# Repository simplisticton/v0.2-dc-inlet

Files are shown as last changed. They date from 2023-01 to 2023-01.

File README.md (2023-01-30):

# Voron V0.2 DC Inlet Foot

Replaces the mains inlet foot part in the V0.2 to allow for the use of an external DC power supply (and consequently a 24V bed heater, since you no longer have mains power on the printer). This is based on the ["Voron 0 DC inlet" mod by arkeet](https://github.com/VoronDesign/VoronUsers/tree/master/printer_mods/arkeet/v0-dc-inlet).

## BOM
- Kycon KPJX-PM-4S connector ([Digi-Key](https://www.digikey.com/en/products/detail/kycon-inc/KPJX-PM-4S/9990081))
- Mean Well GST163A24-R7B power supply ([Digi-Key](https://www.digikey.com/en/products/detail/mean-well-usa-inc/GST160A24-R7B/7703602))
- Power switch, 20mm round, rated for at least 7A at 24VDC ([Digi-Key](https://www.digikey.com/en/products/detail/w-rth-elektronik/471002268142/9950821))
- 2x quick disconnect terminal for power switch ([Digi-Key](https://www.digikey.com/en/products/detail/te-connectivity-amp-connectors/2-520194-2/289254))
- 24V 60W bed heater ([Keenovo](https://keenovo.store/collections/standard-keenovo-silicone-heaters/products/keenovo-square-silicone-heater-3d-printer-build-plate-heatbed-heating-pad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))
- 4x M2x10 self-tapping screw
- 18AWG wire
- Heatshrink tubing

## Implications

There are several implications to not having mains power in your printer:
- 24V bed heater can be safely run at 100% power
- No need for a 24V power supply on the printer itself means a lot more availabe room 
- You can utilize a 24V-5V step down converter to power your Raspberry Pi instead of needing a separate 5V PSU

I recommend using Wago lever nuts and ferules to simplify your wiring and keep it neat and tidy!

## Instructions

1. Prepare the foot as per the Voron V0.2 manual (i.e., insert heatsets).
2. Solder the wires between the Kycon connector and the switch prior to installation. Use the quick-connect terminals on the switch side. Be sure to install heat-shrink tubing over all exposed areas (see figures 2 & 3). Also ensure that the inlet bracket is in place before soldering the connector!
3. Route the bracket, connector, and wires through the switch opening in the DC inlet foot. Don't screw the bracket to the connector until after you've run them through the switch opening -- the connector is a tight fit but if you angle it correctly it will go through! 
4. Screw the inlet bracket to the connector (see figure 4).
5. Snap the switch into place (see figure 5).
6. Screw the inlet bracket into the inlet foot (see figure 6).
7. Connect the switch to your controller board's 24DC in.

## Figures
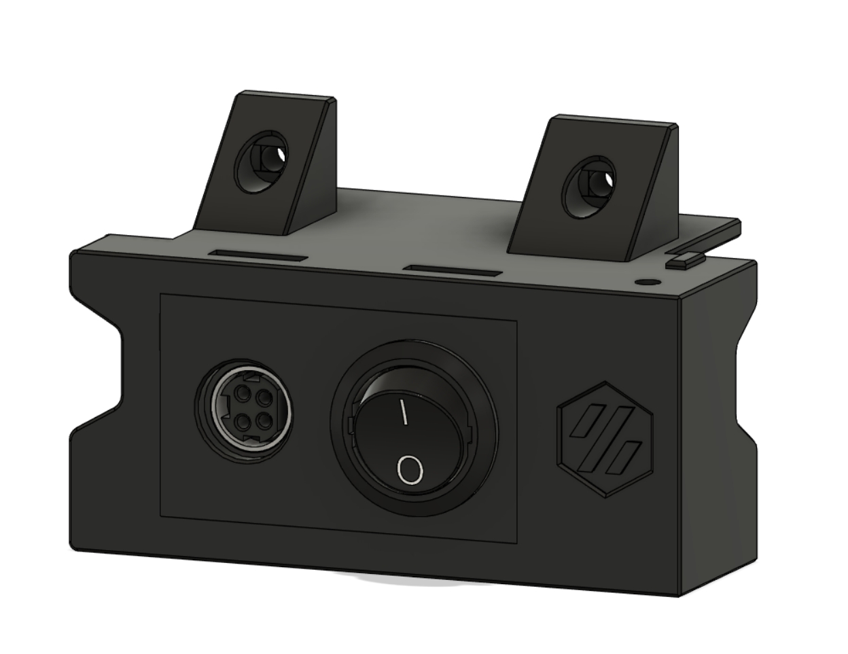
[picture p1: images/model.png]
Figure 1 - model Figure 1: Model

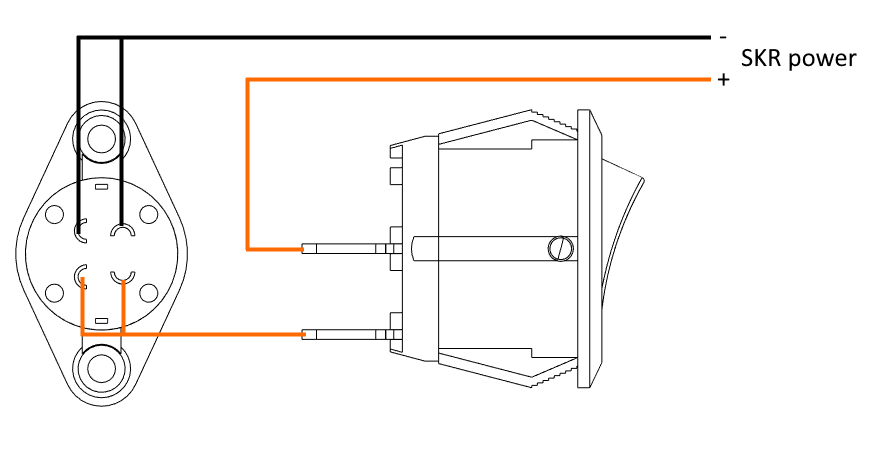
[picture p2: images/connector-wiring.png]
Figure 2 - connector wiring Figure 2: Connector Wiring

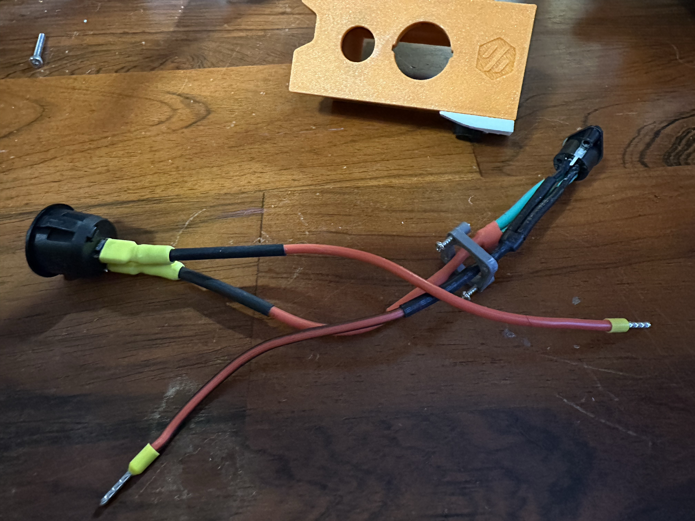
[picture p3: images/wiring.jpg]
Figure 3 - assembled wiring Figure 3: Assembled Wiring

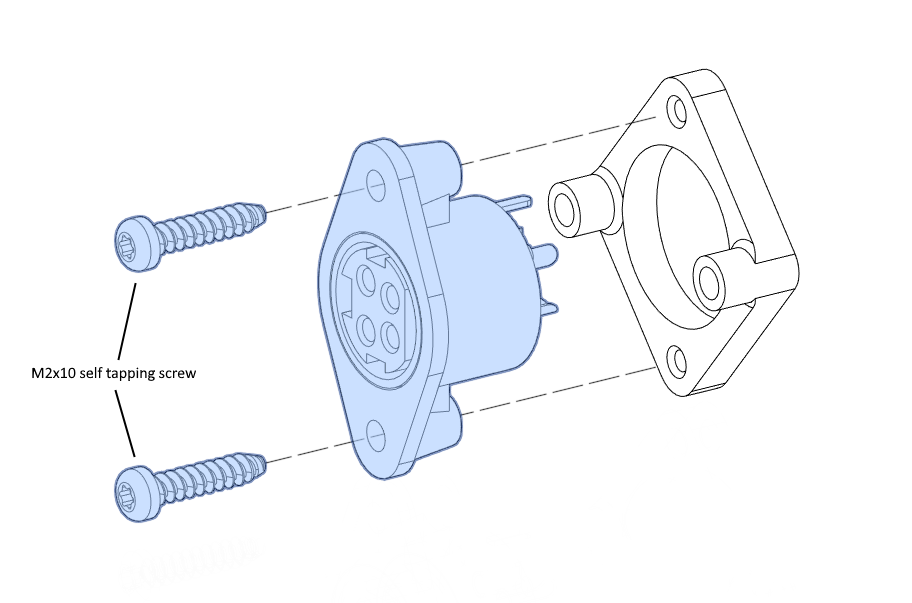
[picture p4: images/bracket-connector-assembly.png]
Figure 4 - bracket-connector assembly Figure 4: Bracket-Connector Assembly

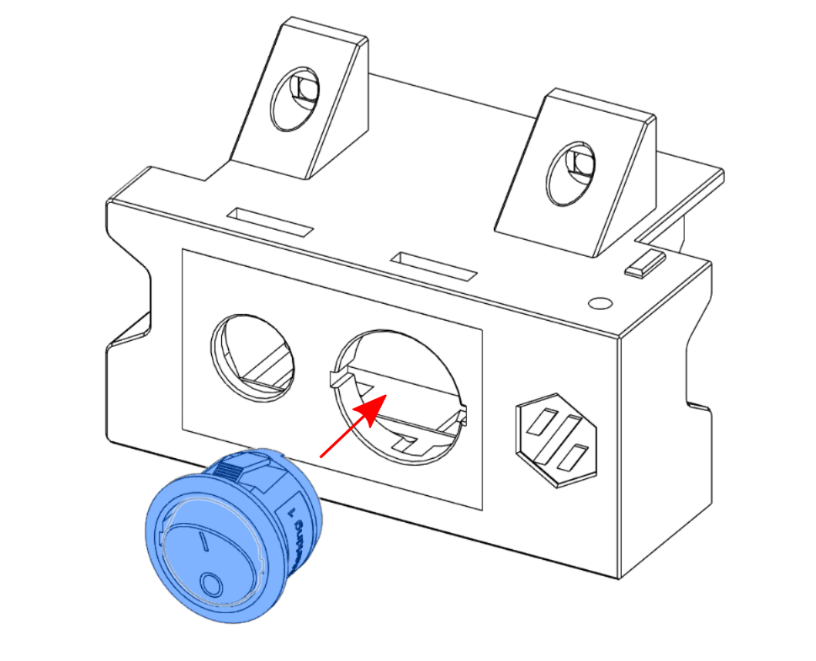
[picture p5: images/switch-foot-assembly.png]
Figure 5 - switch-foot assembly Figure 5: Switch-Foot Assembly

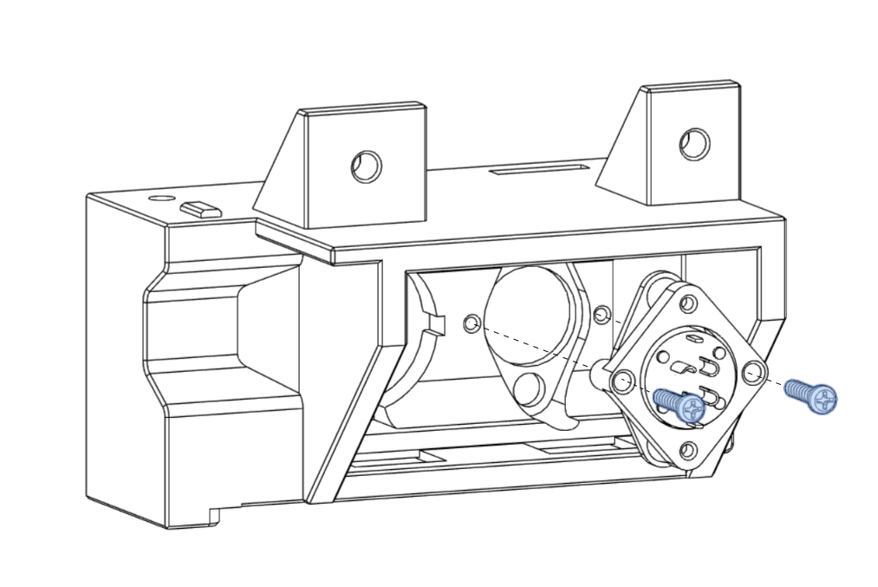
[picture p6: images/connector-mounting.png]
Figure 6 - connector mounting Figure 6: Connector Mounting

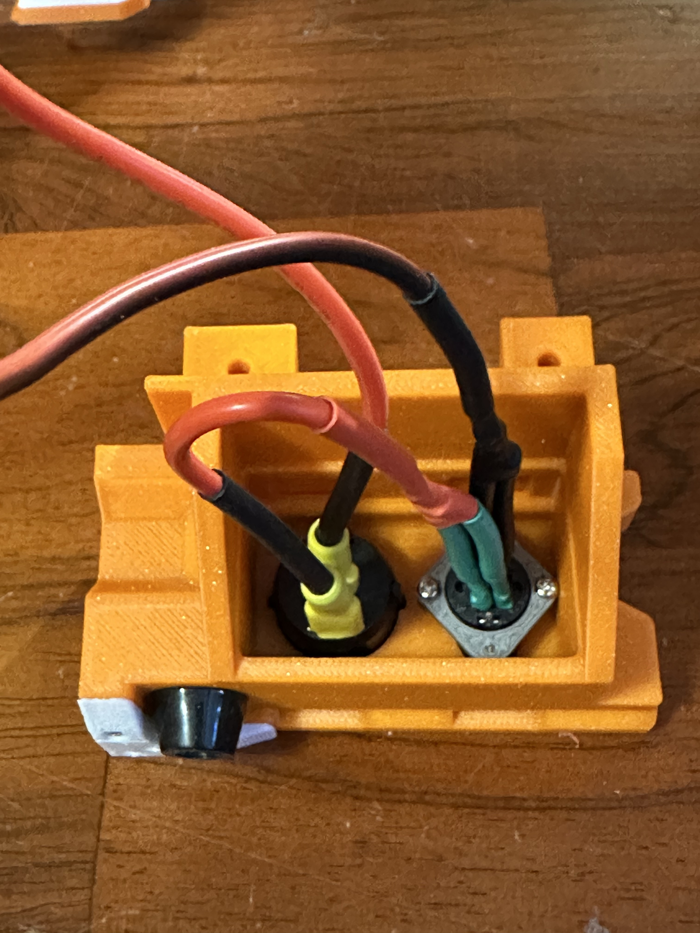
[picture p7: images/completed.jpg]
Figure 7 - completed part Figure 7: Completed part


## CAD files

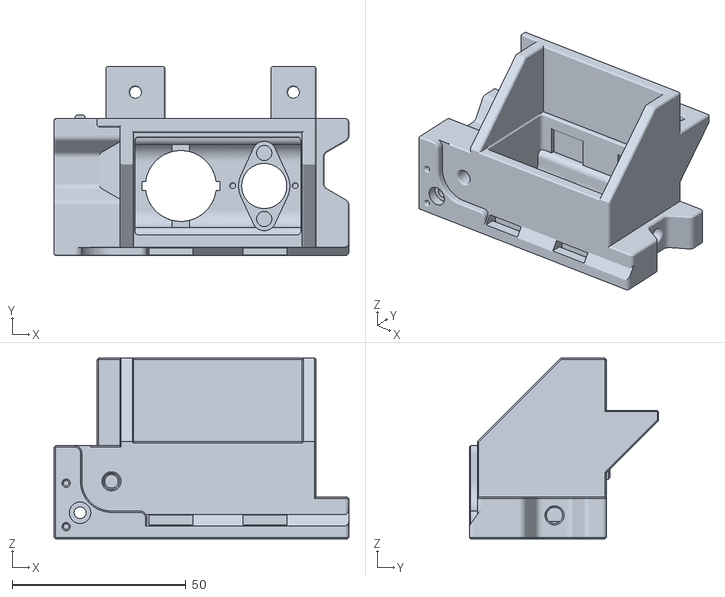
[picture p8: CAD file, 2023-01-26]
STLs/V0-24V-inlet-foot.stl
84.9 x 54.5 x 52.0

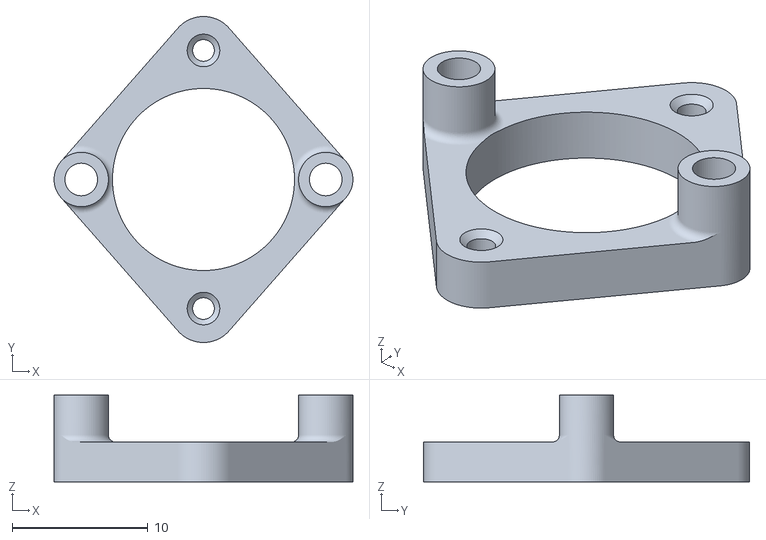
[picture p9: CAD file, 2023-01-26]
STLs/inlet_bracket.stl
22.0 x 24.0 x 6.40

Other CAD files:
CAD/V0.2 24V External PSU Inlet Foot v1.f3d

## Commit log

2023-01-26 add inlet bracket model
    [inlet_bracket.stl]
2023-01-26 switch to STL
    [V0-24V-inlet-foot.stl]
